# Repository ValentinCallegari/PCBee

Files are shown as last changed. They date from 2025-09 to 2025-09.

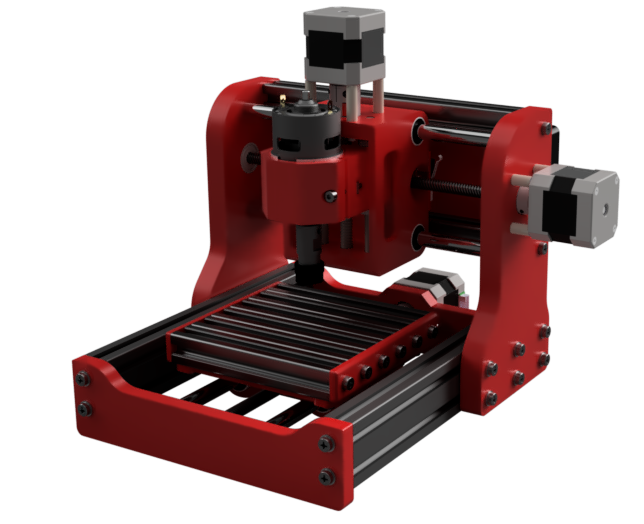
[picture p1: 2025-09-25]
Renders/view 1.png

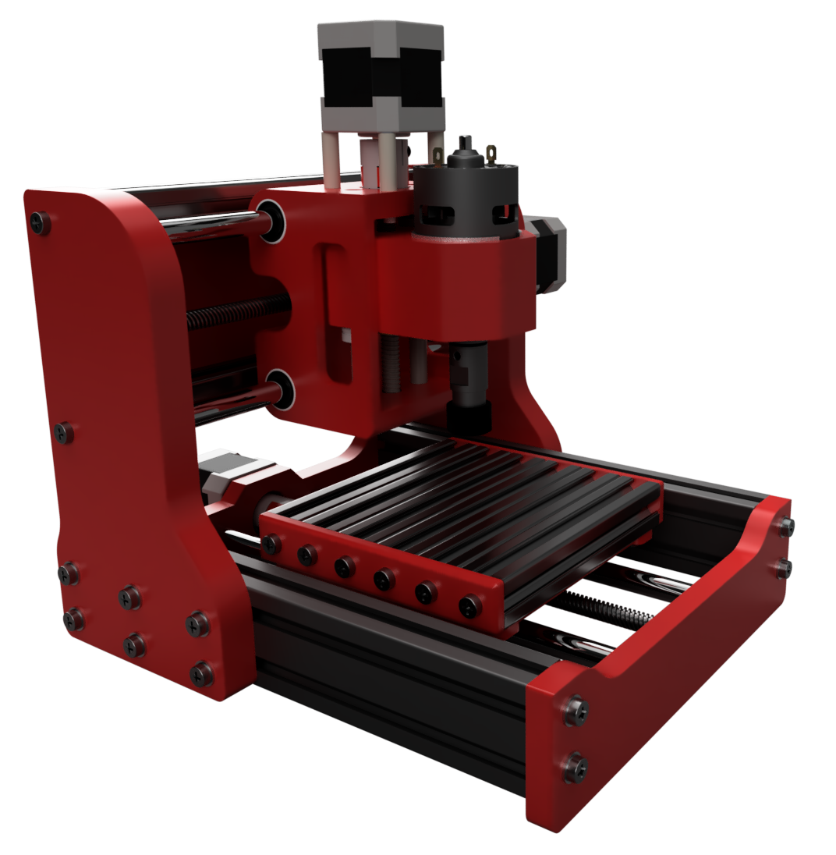
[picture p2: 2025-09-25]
Renders/More View.png

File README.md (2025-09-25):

# PCBee

A small CNC machine for milling PCBs
It can also handle engraving and light milling tasks. 

*Batteries not included.* ⚡

render

---
## ⚠️ Warning

While the machine design is pretty much complete, the **BOM is not fully finalized** and i still have to add some stuff like a proper enclosure for electronics.
Screws, nuts, and other fasteners are not yet listed.  

You can download the provided **CAD files** and check the assembly to get an idea of the exact fasteners required.  

## 📐 Machine Specifications

### Total Machine Size
- **Y:** 290 mm  
- **X:** 285 mm  
- **Z:** 250 mm  

### Work Area
- **X:** 120 mm  
- **Y:** 120 mm  
- **Z:** 25 mm *(Z travel — not including endmill)*  

---

## 🧰 Bill of Materials (BOM)

### Printed Parts
- Can also be **laser-cut, milled, or even cut by hand**. DXF files are provided.  

---

### Extrusion
- 6 × 2020 120 mm *(or 3 × 2040, or 2 × 2060)* → **Bed**  
- 2 × 2040 220 mm → **Chassis**  
- 2 × 2020 200 mm → **X-axis**  

---

### Smooth Rods
- 2 × Ø10 mm × 220 mm → **X-axis**  
- 2 × Ø10 mm × 237 mm → **Y-axis**  
- 2 × Ø8 mm × 100 mm → **Z-axis**  

---

### Bearings
- 8 × LM10UU → **X and Y axis**  
- 4 × LM8UU → **Z axis**  
- 2 × 908 Ball Bearings → **X/Y leadscrew support** *(optional, but looks cool)*  

---

### Other
- 3 × Shaft Couplers *(avoid the "spring" type since those can cause backslash)*  
- 2 × TR8 Leadscrews 210 mm + Anti-Backlash Nuts → **X and Y axis**  
- 1 × TR8 Leadscrew 100 mm + Normal Nut → **Z axis**  

---

## ⚡ Electronics

- 1 × Arduino UNO  
- 1 × CNC Shield  
- 1 × 40×40 12V Fan  
- 1 × 775 Motor + ER11 Collet *(avoid the "drill chuck" type)*  
- 2 × Relay Boards *(optional, used to toggle spindle/aspiration via gcode)*  
- 3 × Stepper Drivers *(A4988 recommended for low cost)*  
- 3 × NEMA 17 Stepper Motors  
- 1 × 12V "Super Slim LED Strip" PSU *(~300W is plenty). Some 775 motors can also work with 24V*  

---

## 🚧 Notes

- Design is intended for **PCB milling**, but it’s versatile enough for engraving and **VERY** light material removal.  
- Many components can be swapped with equivalents depending on what you have on hand.

  FEEL FREE TO FORK AND MODIFY!

---

## 📜 License

[MIT License](LICENSE)

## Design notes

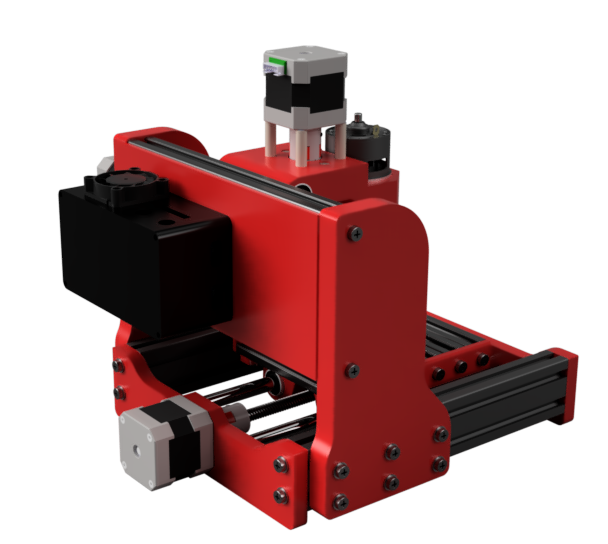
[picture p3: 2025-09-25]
Renders/Rear View.png

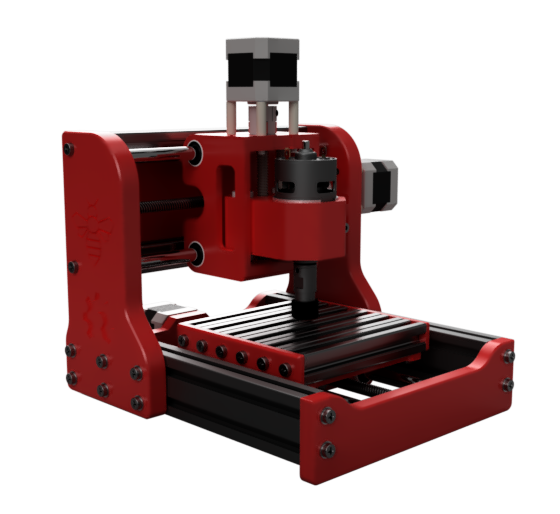
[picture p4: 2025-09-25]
Renders/Side View.png

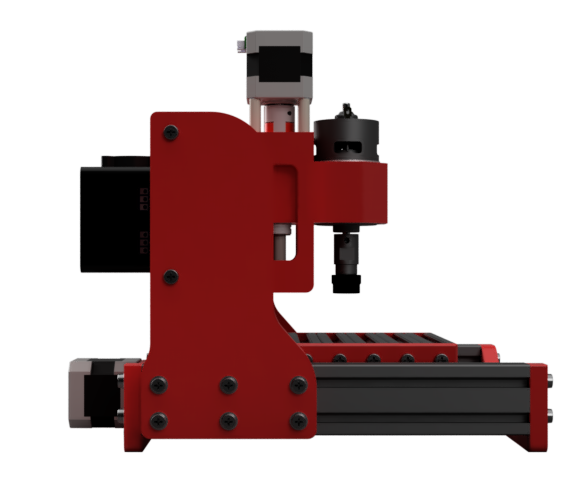
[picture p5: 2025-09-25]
Renders/Side view 2.png

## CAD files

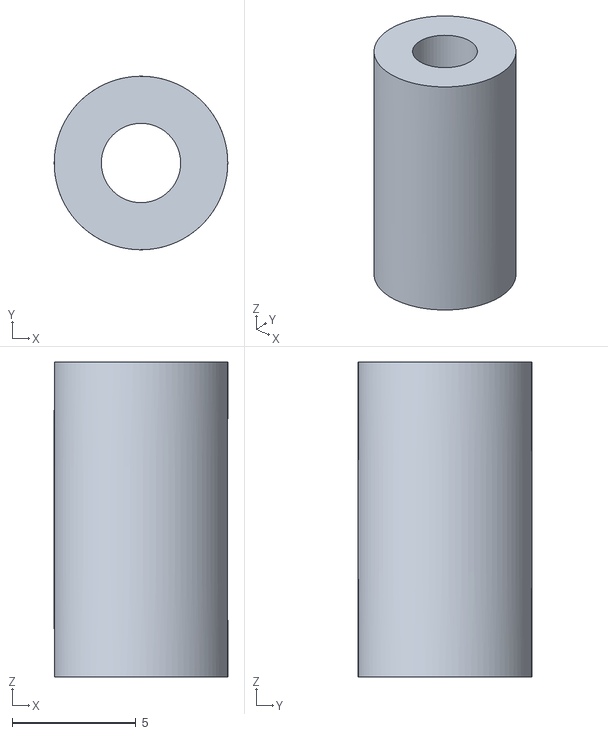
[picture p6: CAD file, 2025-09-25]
STLs/X axis Spacer x4.stl
7.00 x 7.00 x 12.7

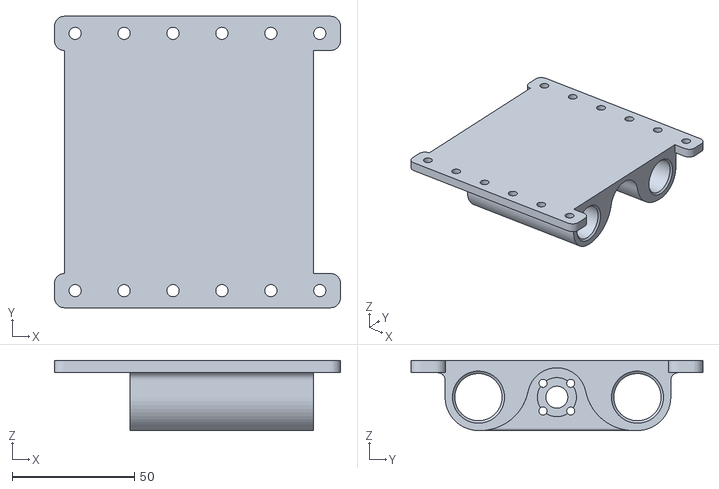
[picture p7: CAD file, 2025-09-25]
STLs/Bed.stl
116.9 x 119.2 x 28.6

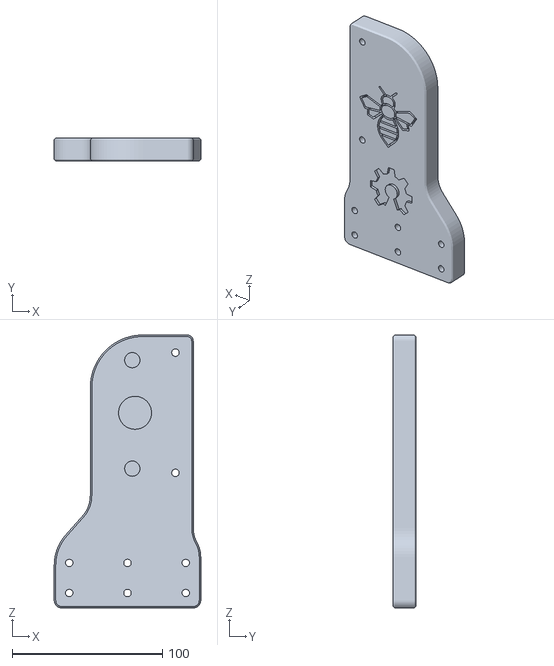
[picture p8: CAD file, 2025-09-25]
STLs/Gantry Left.stl
97.6 x 15.0 x 181.8

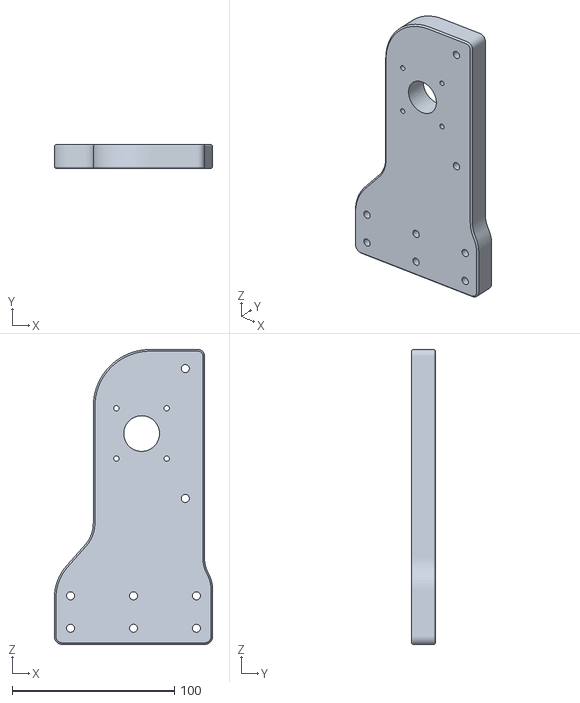
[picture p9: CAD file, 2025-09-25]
STLs/Gantry Right .stl
97.6 x 15.0 x 181.8

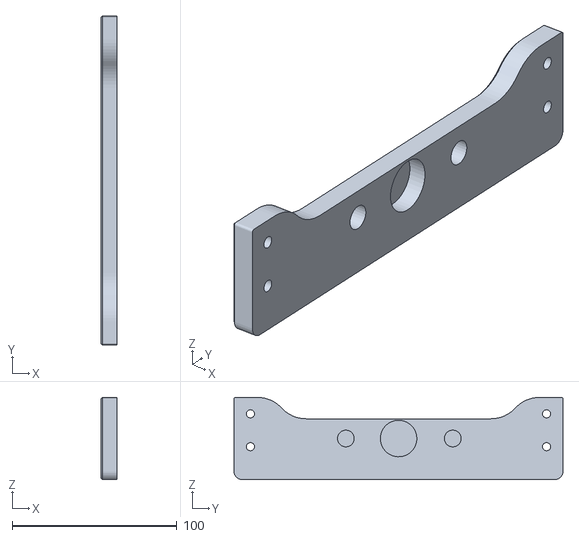
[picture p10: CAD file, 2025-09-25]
STLs/Front Plate.stl
10.0 x 200.0 x 50.0

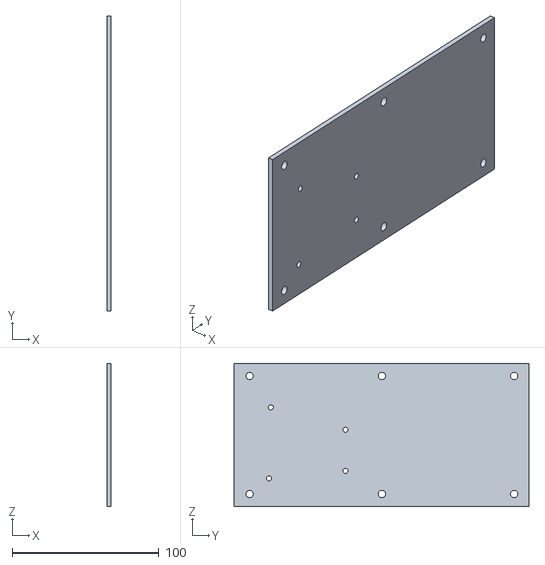
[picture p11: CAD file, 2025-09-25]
STLs/Backplate.stl
3.00 x 200.5 x 97.3

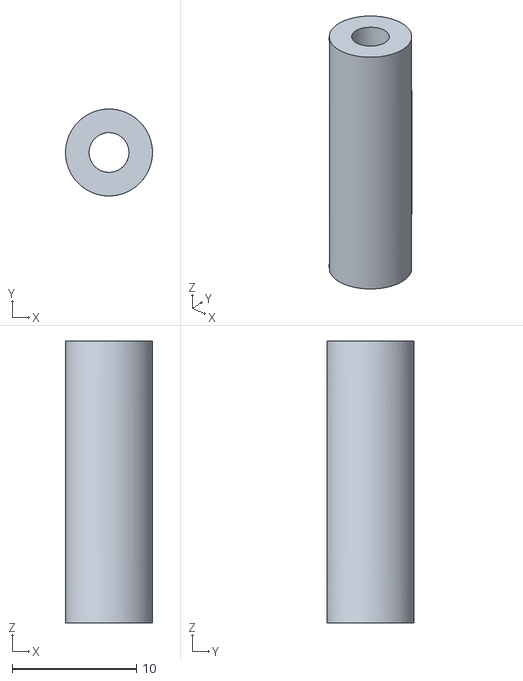
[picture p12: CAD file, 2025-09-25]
STLs/Z Axis Spacer x4.stl
7.00 x 7.00 x 22.7

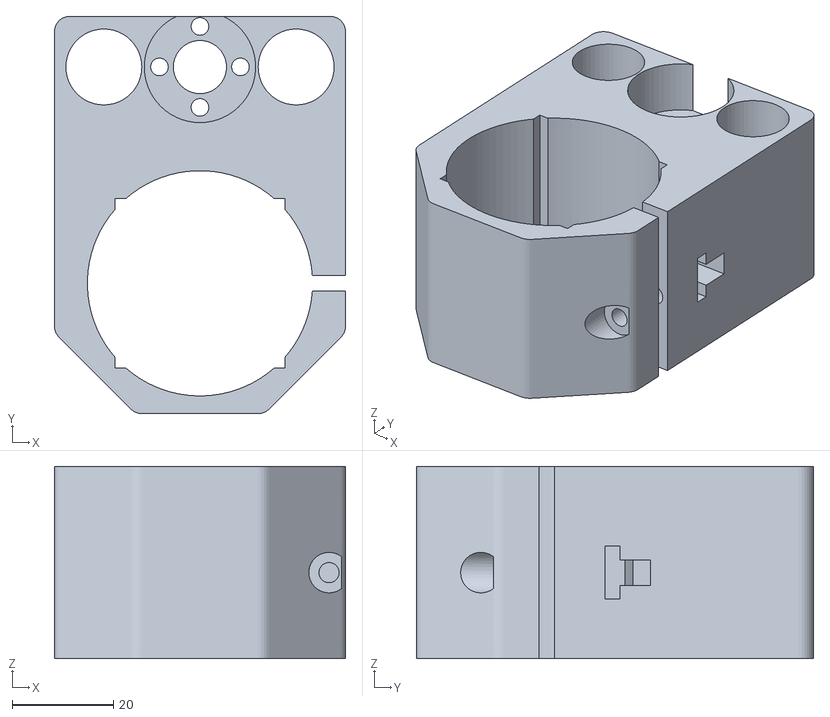
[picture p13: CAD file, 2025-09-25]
STLs/Spindle Clamp.stl
57.5 x 78.5 x 38.0

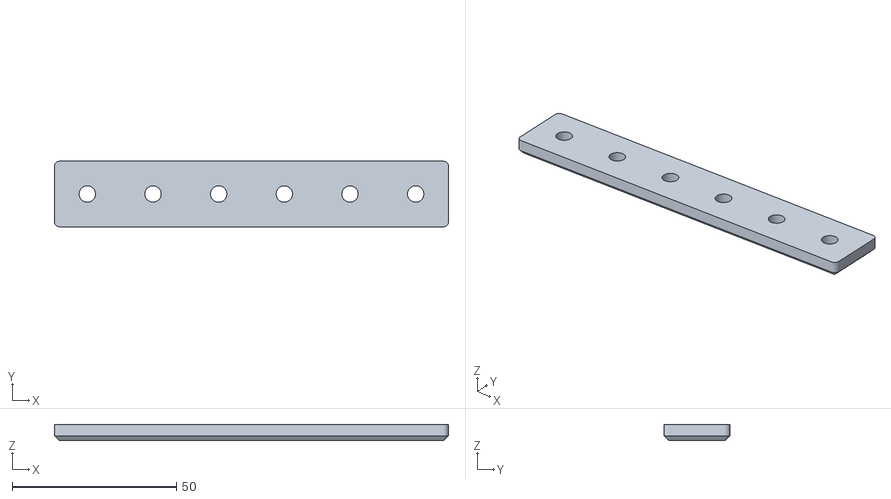
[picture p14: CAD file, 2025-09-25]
STLs/Bed side x2.stl
120.0 x 20.0 x 5.00

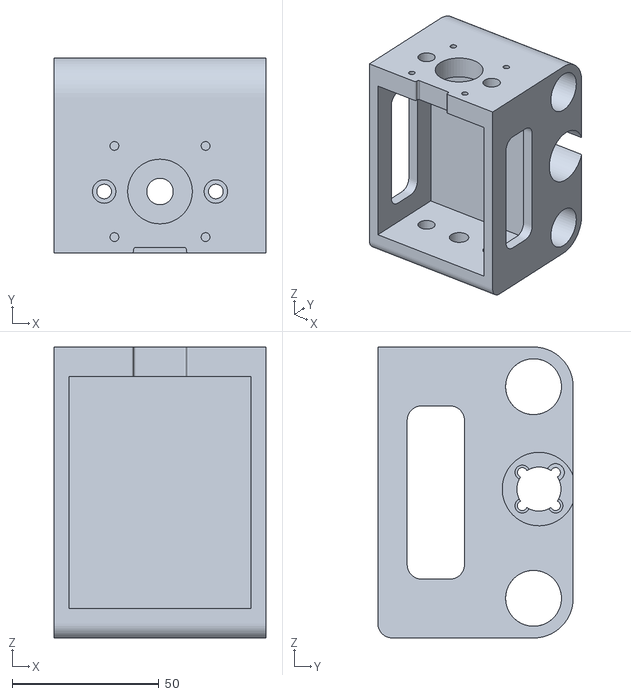
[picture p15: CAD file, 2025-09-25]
STLs/Z Axis body.stl
72.0 x 66.5 x 99.0

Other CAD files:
STLs/Rear Plate.stl
